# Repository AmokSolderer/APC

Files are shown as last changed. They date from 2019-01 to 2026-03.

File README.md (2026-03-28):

# The Arduino Pinball Controller

Before I explain what the APC is, let's first clarify what it is not.
 
The APC is no commercial drop-in replacement board. It is intended for people with some basic knowledge of programming and electronics who want to expand the possibilities of their pinball machine.

As this is a private project with no commercial interest, you may use the APC at your own risk and I'm not liable for any damage that might occur to your machine while using it.  
Some special machines might even not work with the APC or require additional HW. Please check the [Known issues](https://github.com/AmokSolderer/APC#known-issues) section for details.

## Overview

The APC is a freely programmable controller for Williams pinball machines. It uses an Arduino Due and contains all the circuitry required to run a Williams pinball machine from System 3 to System 11c (and the compatible Data East machines):

* Display interface for all corresponding display types
* 24 Solenoid drivers
* Lamp matrix drivers for 64 lamps
* Switch matrix drivers for 64 switches + 8 non matrix switches
* SD card interface (to store audio files, highscores and settings)
* Audio amplifier with two channels (to play music and sound effects simultaneously / can be changed to single channel stereo)

To summarize the above it can be said that the APC does replace all CPU, power driver and sound related boards at a price of well below 100€ per board. 

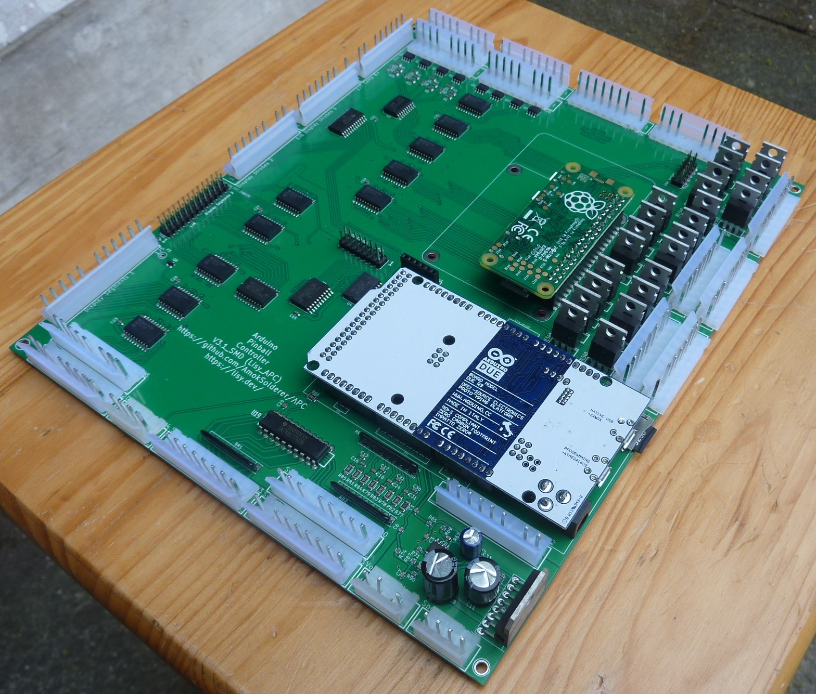
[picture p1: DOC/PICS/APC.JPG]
APC 2.0


The picture shows an APC 3.1 board with the new on-board SD-Card slot below the Arduino.  
See my [APC 3 video](https://www.youtube.com/watch?v=4EgOTJyxMXo) to get an impression what this board can do.

There's a table of contents of the available documentation at the end of this page.

### Special features

* Hardware extensions interface. The pinout is compatible to the Sound Overlay Solenoid Board used in games like Whirlwind, but it is upgraded a bit to support all kind of self made hardware
* A socket for a Raspberry Pi which can be used to run PinMame on the APC board. With this you can run the original ROM code on your APC.
* [PinMameExceptions](https://github.com/AmokSolderer/APC/blob/master/DOC/PinMameExceptions.md) are game specific code blocks that act like a man-in-the-middle between the game HW and PinMame. That means even if your game is running in PinMame you can still introduce some changes. Take a look at my [Jungle Lord video](https://www.youtube.com/watch?v=bbfhH_-gMfE) or my [Comet ball saver](https://youtu.be/JbgMa_pn0Lo) to see how a few lines of code can change a game dramatically.

Typical examples for the use of PinMameExceptions are:

* Pre System11 games usually use just one audio channel which can even be annoying at times. With PinMameExceptions you can add [a background music track](https://github.com/AmokSolderer/APC/blob/master/DOC/PinMameSound_3_7.md#adding-background-music) which replaces the original background sound. The change is easy and for most pre System11 which have PinMameExceptions it's already implemented. Check [this list](https://github.com/AmokSolderer/APC/blob/master/DOC/PinMame.md#available-sounds) for details.
* Add a ball saver. There's a [general ball saver](https://github.com/AmokSolderer/APC/blob/master/DOC/PinMameExceptions.md#how-to-add-a-ball-saver) available which can be easily adapted to your machine. Of course you can also add an individual ball saver - all you have to do is not to tell PinMame that the ball has reached the outhole, but to kick it into the plunger lane instead. Watch my [Comet video](https://youtu.be/JbgMa_pn0Lo) to see how it can be done with just a few lines of code.  
Check the [description](https://github.com/AmokSolderer/APC/blob/master/DOC/PinMameExceptions.md#how-to-add-a-ball-saver) to see how both options work.
* Add HW toys like a shaker motor or flashers and the necessary rules to drive them. If your game has no free solenoid drivers left, then just add the [Solenoid expansion board](https://github.com/AmokSolderer/APC/blob/master/DOC/SolExpBoard.md) to get 8 more. You can also use the [LED expansion board](https://github.com/AmokSolderer/APC/blob/master/DOC/LEDexpBoard.md) to control RGB-LED stripes or just connect your own individual HW.

The picture below shows an APC prototype in my Pinbot.

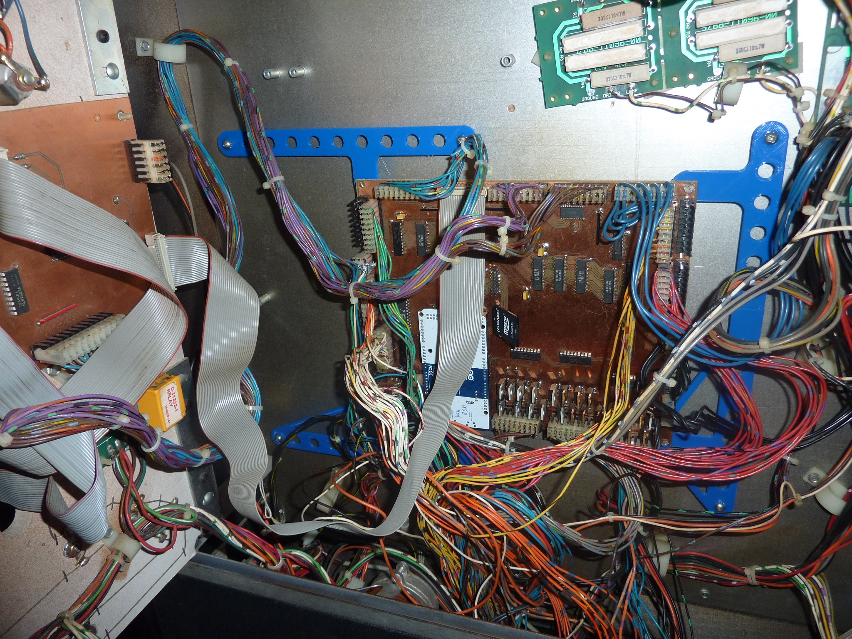
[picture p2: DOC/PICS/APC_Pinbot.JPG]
Pic Pinbot


To see the APC in an early stage you might want take a look at my [Black Knight game video](https://youtu.be/N5ipyHBKzgs)

## Game Software

### PinMame

You can use [Lisy](https://lisy.dev/apc.html) to run PinMame on an APC board. This spares you the effort to do any game Software as you can run the old ROM code.
For System 3 - 7 machines the APC can be used with the old original soundboards. That means in this case it's a plug & play solution.
You might want the APC to generate the audio anyway, either because you don't have an audio board, you want to do your own sounds or you have a System 9 or 11 game. In this case it's going to require some work to set up your game with PinMame. Take a look at the [PinMame Sound page](https://github.com/AmokSolderer/APC/blob/master/DOC/PinMame.md) to see what I mean.

With PinMame running for your game you can use the [PinMameExceptions](https://github.com/AmokSolderer/APC/blob/master/DOC/PinMameExceptions.md) functionality of the APC to change the rules of your game even though it's running under PinMame control.  
Watch my [Jungle Lord video](https://www.youtube.com/watch?v=bbfhH_-gMfE) so see an example. The corresponding code can be found in PinMameExceptions.ino in the AmokPrivate branch on Github.  
Another example is the ball saver I [added to my Comet](https://youtu.be/JbgMa_pn0Lo).

### MPF

For those who want to do their own game rules without having to use C, the APC does support the [Mission Pinball Framework](http://missionpinball.org/). It can run on a PC which then controls the APC via USB.

I did a short video with some basic [MPF setup](https://github.com/AmokSolderer/APC/tree/master/DOC/Software/MPF) to test that everything is working:

[MPF runs APC](https://www.youtube.com/watch?v=w4Po8OE5Zkw)

### C code

If you're familiar with C you can also program the APC directly. This SW would then run on the Arduino itself with no need for an additional PC or Raspberry Pi.  
For this the APC software offers an [API](https://github.com/AmokSolderer/APC/blob/master/DOC/Software/APC_SW_reference.pdf) providing the necessary commands to control a pinball machine. It's still a lot of effort to program a game completely from scratch, but you could even run your game in PinMame and only use the API to do changes or extensions to the original rules.

You don't necessarily have to do the code from scratch. There is a [Base Code](https://github.com/AmokSolderer/APC/blob/master/BaseCode.ino) which covers the basics of a pinball machine and can be used as a starting point.  
Furthermore there're the above mentioned [PinMameExceptions](https://github.com/AmokSolderer/APC/blob/master/DOC/PinMameExceptions.md) which can change a game dramatically with just a few lines of code.

## Hardware

The APC hardware status is mature. I have version 2.0 in use since January 2018 without anything to complain about. Since then the HW has basically stayed the same, just some features have been added and the board has been prepared for automatic assembly.
You can find the schematics, BOM and layout data in the [hardware section](https://github.com/AmokSolderer/APC/tree/master/DOC/Hardware). There have been some minor HW updates which are explained in the [Changelog](https://github.com/AmokSolderer/APC/blob/master/DOC/Changes.md).

The APC features an HW extensions interface which is an 8 bit bus with several enable signals. At the moment there're two extension board available, but you could use it for all kinds of additional hardware.

The first board is an LED expansion board to control WS2812 based LED-Strips with the APC. For more information about this board please refer to the [APC LED expansion board](https://github.com/AmokSolderer/APC/blob/master/DOC/LEDexpBoard.md) section.

The following picture shows the APC in a Comet with the LED Expansion board connected to the hardware extensions interface.

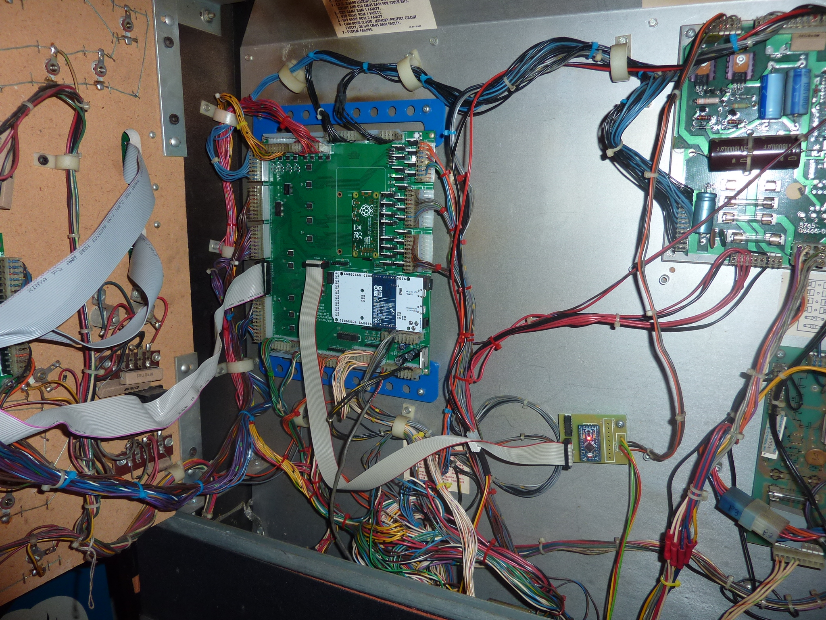
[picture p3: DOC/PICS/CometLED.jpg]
APC Comet LED


A short video with this setup can be found here : 

[GI LEDs](https://youtu.be/kLWVUdhSwfo)

The second board is a [driver for 8 additional solenoids](https://github.com/AmokSolderer/APC/blob/master/DOC/SolExpBoard.md). The current version is mainly suited for use with an own power supply (e.g. for 24V shaker motors).

I use [special alphanumerical displays](https://github.com/AmokSolderer/APC/blob/master/DOC/Sys7Alpha.md) in my Black Knight which can also be found in the HW section as well as an LED replacement for the original System7 numerical displays.

## Supported machines

The following table gives an overview about the various system generations the APC can be used with and if at least one machine of each generation has been confirmed to work with it. Additionally you can see whether PinMame or [MPF](http://missionpinball.org/) have been tested with at least one machine of this generation and whether some special preparation like additional cables are required. Details about these cables can be found [here](https://github.com/AmokSolderer/APC/blob/master/DOC/HowToStart.md#cable-extensions)

The PinMame support is still under development and even if a generation is basically supported you still need the audio files for your particular game. A list of available audio files and a description how to extract your own files can be found on the [PinMame page](https://github.com/AmokSolderer/APC/blob/master/DOC/PinMame.md).

| Williams System | Tested  | PinMame support | MPF support | Comment |
|--|--|--|--|--|
|3| Yes | Yes | Yes|When PinMame is used, some solenoid activation times need to be increase by a [PinMameException](https://github.com/AmokSolderer/APC/blob/master/DOC/PinMameExceptions.md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)|
|4| Yes | Yes | Yes|When PinMame is used, some solenoid activation times need to be increase by a [PinMameException](https://github.com/AmokSolderer/APC/blob/master/DOC/PinMameExceptions.md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)|
|6| Yes | Yes | Yes |When PinMame is used, some solenoid activation times need to be increase by a [PinMameException](https://github.com/AmokSolderer/APC/blob/master/DOC/PinMameExceptions.md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)|
|7| Yes | Yes | Yes | Needs two additional wires |
|9| Yes | Yes | Yes |  |
|11| Yes | Yes | Yes |  |
|11a| Yes | Yes | Yes | Some cable ties have to be cut and the wiring harness opened a bit |
|11b| Yes | Yes | Yes | Some cable ties have to be cut and the wiring harness opened a bit |
|11c| Yes | Yes | Yes | The wires of three connectors must be extended |

The following Data East MPUs are almost identical to their counterparts from Williams but DE used 2.1 audio boards. Check the [known issues](https://github.com/AmokSolderer/APC#known-issues) for details

| Data East Version | Tested  | PinMame support | MPF support | Comment |
|--|--|--|--|--|
|1| Not yet | Yes | Yes | audio needs a cable adapter and is only mono |
|2| Not yet | Yes | Yes | audio needs a cable adapter and is only mono |
|3| Yes | Yes | Yes | Only non DMD machines / audio needs a cable adapter and is only mono / probably some [cable extensions](https://pinside.com/pinball/forum/topic/arduino-pinball-controller/page/18#post-6846714) are needed |

## Changes / What's new?

A history of the recent changes can be found in the [Changelog](https://github.com/AmokSolderer/APC/blob/master/DOC/Changes.md)

## Known issues

### Stereo audio

Some games like Jokerz! or Data East games starting from MPU version 1 have stereo or even 2.1 audio boards. These are currently not supported by the APC SW.  
From the HW point of view, the APC is capable of generating two independent sound channels which could also be used for stereo. But up to now they're used to generate separate channels for sounds and music which are combined in the output amplifier.  
In order to use these machines with the APC you'd have to build a cable adapter and the audio would only be mono.

### Stepper motors

Games like Jokerz! or Riverboat Gambler use stepper motors to drive a wheel in the backbox and the amount of steps being generated determine where the wheel stops.  
Alas, there's a problem with Lisy/PinMame not sending all steps to the APC. This means it is not possible for the APC to determine at which position the wheel is supposed to stop.  
Note that this is not a problem of the APC itself, but occurs only when Lisy/PinMame is used. If you program your game code in C there won't be any problems.

### Rollergames music problems

The Rollergames implementation in PinMame has a bug in the music control. For some reason a new music track is started every few seconds. Most of the time it's the same track that's already running. I have therefore implemented a workaround in the PinMameExceptions of the Rollergames which prevents that the running music track can be restarted. This improves the situation somehow, but more sophisticated PinMameExceptions are needed to really fix this.  
Up to now only Rollergames seems to be affected, other machines using the same audio boards are working fine.

## Feedback

Feedback is very important for me, also to learn where additional documentation is needed. There're still features that are undocumented because I just don't have the time (and motivation) to write the docs.  
Hence, I've limited my documentation effort to a minimum, but I'm willing to provide additional docs and hints on request. Please use the forum links below for these requests.  

**So if you're interested please leave some feedback in the [Flippertreff forum (german)](https://www.flippertreff.de/start/forum/topic/11356-arduino-pinball-controller/) or in the  - [Pinside Form (english)](https://pinside.com/pinball/forum/topic/arduino-pinball-controller#post-4898318).**

## How to get startet?

I'm sorry, but I'm not going to sell any boards. Check whether anyone in the above mentioned forums has a spare board for sale. If this fails you can still order populated boards from China.  
If you're interested in using an APC, then be sure to follow the instructions given in the first part of the documentation listet below. They will guide you through the process of getting and setting up an APC board.

## Documentation contents

1. Building and setting up an APC  
1.1. [The APC board](https://github.com/AmokSolderer/APC/blob/master/DOC/APC_board.md) - How to get one and how to set it up  
1.2. [Upload the SW](https://github.com/AmokSolderer/APC/blob/master/DOC/Upload_SW.md) - How to program the Arduino DUE  
1.3. [Basic Preparation](https://github.com/AmokSolderer/APC/blob/master/DOC/Prepare.md) - Required cables and stuff  
1.4. [Do the tests](https://github.com/AmokSolderer/APC/blob/master/DOC/InitialTests.md) - Test your board  
1.5. [Run a game](https://github.com/AmokSolderer/APC/blob/master/DOC/RunGame.md) - All the ways to get a game running  

2. References  
2.1. [Setting up the BaseCode](https://github.com/AmokSolderer/APC/blob/master/DOC/SetUpBC.md) - Do the BaseCode setup to get a very simple game  
2.2. [Useful software tools](https://github.com/AmokSolderer/APC/blob/master/DOC/UsefulSWtools.md) - Simple tools for audio data conversion and so on  
2.3. [APC settings](https://github.com/AmokSolderer/APC/blob/master/DOC/Settings.md) - a table of the settings and how to use them  
2.4. [APC schematics](https://github.com/AmokSolderer/APC/blob/master/DOC/Hardware/APC_schematics.pdf) - just in case you want to know what you're about to build  
2.5. [If things don't work](https://github.com/AmokSolderer/APC/blob/master/DOC/Problems.md) - If you have a problem, check here first  
2.6. [APC specialties](https://github.com/AmokSolderer/APC/blob/master/DOC/Specialties.md) - How special switches and the flipper relay are handled by the APC

3. Writing my own game code - You want to program your own game in C? Then read this.  
3.1. [Game code tutorial](https://github.com/AmokSolderer/APC/blob/master/DOC/GameCodeTutorial.md) - A step by step introduction to writing your own game code  
3.2. [APC software reference](https://github.com/AmokSolderer/APC/blob/master/DOC/Software/APC_SW_reference.pdf) - All commands of the API in a nutshell  

4. Running PinMame  
4.1. [Lisy Homepage](https://lisy.dev/apc.html) - Location of the Lisy SW download and more  
4.2. [PinMame Sound](https://github.com/AmokSolderer/APC/blob/master/DOC/PinMame.md) - shows whether your game is supported and what to do if not  
4.3. [PinMame System 3 - 7 Sound howto](https://github.com/AmokSolderer/APC/blob/master/DOC/PinMameSound_3_7.md) - How to enable the sound of System 3 - 7 games  
4.4. [PinMame System 9 Sound howto](https://github.com/AmokSolderer/APC/blob/master/DOC/PinMameSound_9.md) - How to enable the sound of System 9 games  
4.5. [PinMame System 11 Sound howto](https://github.com/AmokSolderer/APC/blob/master/DOC/PinMameSound_11.md) - How to enable the sound of System 11 games  
4.6. [PinMameExceptions](https://github.com/AmokSolderer/APC/blob/master/DOC/PinMameExceptions.md) - change your game, but let PinMame do the main work  
4.7. [PinMame game numbers](https://github.com/AmokSolderer/APC/blob/master/DOC/lisyminigames.csv) - list of the PinMame game numbers  
4.8. [Controlling Lisy](https://github.com/AmokSolderer/APC/blob/master/DOC/LisyDebug.md) - updating Lisy and using the debug mode  
4.9. [Automatic sound file generation](https://github.com/AmokSolderer/APC/blob/master/DOC/SoundAuto.md)  
5.0. [Manual sound file generation](https://github.com/AmokSolderer/APC/blob/master/DOC/SoundManual.md)  
5.1. Another way [for extracting sound files](https://github.com/AmokSolderer/APC/blob/master/DOC/PinMameSounds.md) - automatic extraction of sound files and the use of Audacity in more detail (by Mokopin)

5. Using MPF  
5.1. [MPF runs APC](https://www.youtube.com/watch?v=w4Po8OE5Zkw) - see my first humble MPF steps in this video  
5.2. [MPF setup](https://github.com/AmokSolderer/APC/tree/master/DOC/Software/MPF) - my MPF test config files

6. Additional APC hardware - boards and other stuff that might come in handy with the APC  
6.1. [APC LED expansion board](https://github.com/AmokSolderer/APC/blob/master/DOC/LEDexpBoard.md) - a board to control WS2812 based LED strips with the APC  
6.2. [APC solenoid expansion board](https://github.com/AmokSolderer/APC/blob/master/DOC/SolExpBoard.md) - to control additional features  
6.3. [System 7 alphanumeric display](https://github.com/AmokSolderer/APC/blob/master/DOC/Sys7Alpha.md) - to have alphanumerical displays in a pre System 11 machine  
6.4. [Installation frames](https://github.com/AmokSolderer/APC/blob/master/DOC/Frames.md) - to mount the APC in your backbox  

7. Additional non APC hardware - just some stuff I designed over the years. Can also be used without the APC  
7.1. [System 7 LED display](https://github.com/AmokSolderer/APC/blob/master/DOC/DispSys7.md) - an LED replacement display for System 7, purely numerical  
7.2. [System 11 LED display](https://github.com/AmokSolderer/APC/blob/master/DOC/DispSys11.md) - an LED replacement display for System 11  
7.3. [System 11a LED display](https://github.com/AmokSolderer/APC/blob/master/DOC/DispSys11a.md) - an LED replacement display for System 11a and early 11b  
7.4. [System 11b LED display](https://github.com/AmokSolderer/APC/blob/master/DOC/DispSys11b.md) - an LED replacement display for later System 11b and 11c  

8. APC games - Complete games running natively on the APC or games that run in PinMame but have been changed  
8.1. [Black Knight](https://github.com/AmokSolderer/APC/blob/master/DOC/BlackKnight.md) - Complete game code with some additional features  
8.2. [Pinbot](https://github.com/AmokSolderer/APC/blob/master/DOC/Pinbot.md) - Complete game code with some additional features  
8.3. [Comet](https://github.com/AmokSolderer/APC/blob/master/DOC/Comet.md) - Some extensions to the original game code running in PinMame

9. Videos - For the generation Youtube  
9.1. [What's new in APC3](https://youtu.be/4EgOTJyxMXo) - Gives an overview about what the APC is and what version 3 can do  
9.2. [Lisy, APC and PinMame](https://youtu.be/cXrh-XPqCKw) - Shows the use of PinMame in an early stage  
9.3. [PinMameExceptions](https://youtu.be/bbfhH_-gMfE) - What is a PinMameException and how does it work?  
9.4. [Adding a ball saver with PinMameExceptions](https://youtu.be/JbgMa_pn0Lo) - Another example of how to use PinMameExceptions  
9.5. [APC MPF](https://youtu.be/w4Po8OE5Zkw) - A simple demonstration of the APC being controlled by MPF  
9.6. [GI LEDs](https://youtu.be/kLWVUdhSwfo) - Shows the LED_exp board in action  
9.7. [Arduino Pinball Controller hardware extensions interface](https://youtu.be/8BnVTpKq-2Y) - Also shows the use of the LED_exp board, but in an early SW stage  
9.8. [APC Black Knight demo](https://youtu.be/N5ipyHBKzgs) - My first APC video. Not really up to date any more, but it shows the basics  
9.9. [How to use numerical displays](https://youtu.be/2A5Tt9FQ2as) - How to navigate the menus when you can't read any text  
9.10. [How to adjust the display setting to a 2x16 alphanumerical display](https://youtu.be/XqPWbm-HWM8) - How to find the right setting to make these displays work

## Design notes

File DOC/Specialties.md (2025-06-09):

# APC specialties

Usually the APC handles the pinball hardware quite straightforward. That means the lamp, switch and solenoid numbers used by the APC are the same as printed in the manual of your pinball machine, no matter whether you use MPF, Lisy/PinMame or write your own C code.  
However, there're some specialties which are handled in this section.

## Special switches

Williams assigned numbers only to Switches which belong to the switch matrix.  
The APC assigns numbers > 64 to the rest of them, so they can be used as normal switches:

| APC switch number | Williams equivalent |
|--|--|
| 65 | Activation switch for special solenoid 1 |
| 66 | Activation switch for special solenoid 2 |
| 67 | Activation switch for special solenoid 3 |
| 68 | Activation switch for special solenoid 4 |
| 69 | Activation switch for special solenoid 5 |
| 70 | Activation switch for special solenoid 6 |
| 71 | Memory Protect switch |
| 72 | Advance switch |
| 73 | Up/Down switch (active when the switch is in Up position) |

Additional information about these switches is provided below:

### Special solenoids and their switch numbers

Williams machines from System3 to System 11a have so called special solenoids. Each of these solenoids is connected to a special switch which will fire the solenoid immediately without any involvement of the CPU. This means that those special switches are not part of the switch matrix (which is CPU controlled). They are handled by a dedicated logic, are not visible for the CPU and therefore have no numbers.  
If your switch matrix has a switch for a special solenoid anyway, then it's because the CPU needs to know when it is triggered (e.g. for scoring). It's a second switch additional to the special solenoid switch. For example: in case of a pop bumper, the plastic disc to trigger the bumper is usually connected to the special solenoid switch and the scoring switch is triggered by the bumper ring being pulled down by the solenoid.  
This means that you have to select the special solenoid switch as the activation switch for your pop bumper, because the scoring switch is only activated when the solenoid is already moving.

The APC handles special solenoid switches as normal switches, but their numbers start with 65 which is the trigger switch for special solenoid 1.  

Williams dropped the special solenoid switches with the start of System 11b. After that the activation switches were part of the switch matrix and controlled by the CPU.

### The Advance, Memory Protect and Up/Down switch

Similar to the special solenoid switches, the Advance, Memory Protect and Up/Down switch are also not part of the switch matrix. The APC assignes the numbers > 70 to them. Note that the Up/Down switch is low active, which means that it's active when NOT pressed.

## The flipper relay

In the original Williams HW the flipper relay switches both flipper fingers at once and has no solenoid number.  
The APC doesn't use a relay but switching transistors. There's one for the left and one for the right flippers, so it is possible to activate the sides individually.  
Their solenoid numbers are 23 and 24, but any (de-)activation command sent to solenoid 25 will affect both flipper fingers.

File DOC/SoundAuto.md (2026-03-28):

# Automatic sound file generation

## Automatic extraction from PinMame

In PinMame, press F4 to enter the 'Sound Command Mode' then press DEL for the Manual / Command Mode.

Now enter the audio command you want PinMame to start with, for audio board 0 this would be 000000000000 and 000000000100 for audio board 1. Press F6 to start the automatic extraction. PinMame will go through the audio command one by one and generate .wav files of them.  
This should generate most of the sound files, but there're limits especially for System11. The music files for example are sometimes truncated, so you'd have to extract them manually. This is not a big deal because there're just a few of them, usually starting with the audio command 000000000101.  
Another problem with early System11 is that PinMame cannot find all sounds for audio board 1. You could try to guide it by using additional start commands like 000000000160, but it's easier to just leave it for now and if you get an error message like '1_85.snd not found' during your first games then you know that starting another extraction with 000000000180 should do the trick.

## Automatic renaming

Files generated with this method get names which include the audio command number and the machine name (e.g. 0x00A5-fire_l3.wav). However, the APC needs the names in the format [single digit board prefix]_[sound number in hex].wav, so the correct name for this sound would be 0_a5.wav. With Linux you can just use the rename command which should be part of most distributions and is very powerful. Windows users would have to install some bulk renaming tool.  
On our case we need to use

    rename -v -n 's/0x00//' *         to remove the '0x00' at the start of the filename
    rename -v -n 's/-fire_l3//' *     to get rid of the rom name
    rename -v -n 'y/A-Z/a-z/' *       to replace upper case by lower case letters
    rename -v -n 's/^/0_/' *          to add the board prefix '0_'

The actions will be done for all files in the current directory. Note that the -v -n options will issue a dry run, so the tool will just show you the new names without actually doing anything.

## Automatic processing with Audacity

Basically you have to do the same steps as described in the [manual way of sound file preparation](https://github.com/AmokSolderer/APC/blob/master/DOC/SoundManual.md), but you'd use a macro to process all files in your working directory. An example macro for processing callouts would look like this:

    Select:End="0,15" Mode="Set" RelativeTo="ProjectStart" Start="0"
    Delete:
    Select:End="0" Mode="Set" RelativeTo="ProjectEnd" Start="0,05"
    Delete:
    SelectAll:
    Normalize:ApplyGain="1" PeakLevel="0" RemoveDcOffset="1" StereoIndependent="0"
    Amplify:Ratio="1,9952623"
    ExportWav:
    
This will delete 150ms at the beginning, as the automatic extraction sometimes adds a few ms of noise to the start of a sound and 50ms at the end. Then it normalizes the sound to a peak level of 0dB and amplifies even 6dB more. The latter will cause the signal to be distorted, but it's still OK as it will just affect the peaks and callouts need to be quite loud to be still audible when the BG music plays.

These are just example values I used for one specific machine. You generally have to find out for yourself what the best relation in terms of volume is for the BG music, the callouts and the general sound effects.

## Sampling Rate

Windows users will additionally have to set the sampling rate to the standard 44.1KHz, as the Windows PinMame uses 48KHz by default. This cannot be batched processed in Audacity, so you'd have to use a tool like [OCENAUDIO](https://www.ocenaudio.com) for this.

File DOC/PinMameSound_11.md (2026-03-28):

# System 11

The first System11 machines had two independent audio circuits, each containing a processor and sound EPROMS. One of these circuits was located on the main CPU board while the other was on a seperate audio board. PinMame distinguishes these boards by using two audio prefixes which can be selected by 00 and 01 in PinMame's 'Sound Command Mode'. Both of these prefixes offer different sound commands.
The table below shows the special commands of the Pinbot audio system that we know about. There might still be some gaps, but it's enough to make the Pinbot work.  
So if you have additional information to fill these gaps please tell us and we're going to include it.

For this documentation I expect the other System 11 machines to work in a similar way.

|Prefix|Command / Hex|Comment|
|--|--|--|
|00|00|Stop Sound|
|01|00|Stop Music|
|01|01 - 08|Looped music tracks, some of them have an intro before the looping part begins|
|01|40 - 42|Transistions and endings for looped music|
|01|7f|Stop sounds of prefix 01|
|01|6X|Music volume setting 0x60 is full volume 0x64 is almost nothing|

## Sound files

There're multiple ways to obtain the original sounds for System 11 machines. Some can be found on the internet, directly recorded from your pinball machine or you can extract them from PinMame. What ever you do, the result should be a mono WAV file with 44.1KHz sampling rate and reasonable amplitude.  
If you find the files on the internet you can proceed to the [Audio file conversion](https://github.com/AmokSolderer/APC/blob/master/DOC/PinMameSound_11.md#audio-file-conversion) section, as you don't have to extract them from PinMame.

## Automatic sound file preparation

There're several methods to automatically extract WAV files from PinMame and batch process them to work with the APC. Using this, it just takes me 2 - 3 hours to generate the files for an early System11 machine  
My way of doing this is described [here](https://github.com/AmokSolderer/APC/blob/master/DOC/SoundAuto.md). Since I'm using Linux, things might be a bit different for Windows users, as they additionally have to adjust the sample rate for example.  
Mokopin (from the Flippertreff forum) has also written some [Instructions for extracting sound files](https://github.com/AmokSolderer/APC/blob/master/DOC/PinMameSounds.md) which explain the automatic extraction of sound files and the use of Audacity for Windows users.

## Manual sound file preparation

This decribes the [manual way of sound file preparation](https://github.com/AmokSolderer/APC/blob/master/DOC/SoundManual.md). I'd recommend to try the automatic way first, because it's much faster. However, the manual way explains what needs to be done and it can be used as a fallback solution, if the automatic way fails. This is usually happens for the music themes of System11 machines. The automatic extraction often truncates those, so these would have to be extracted manually. System11 music themes usually consist of an intro and a looping part, s I'd recommend to manually extract a long music file and use Audacity to split it up accordingly. The correct naming for such music themes will be handled the PinMameExceptions section below.

## Volume levels

Callouts are sensitive and need to be quite loud in order not to get lost in the music. Hence, it makes sense to load a music theme and a callout into Audacity and play them simultaneously. I usually amplify the callouts to +6dB (accepting the minor distortion caused by this) and choose the volume of the music themes as high as possible for the callout to still sound well. The other sounds can usually have the same volume level as the BG music.

## Audio file conversion

Put all preprocessed WAV files in one folder, check that the names are correct and execute the [AudioSaveFolder.pl](https://github.com/AmokSolderer/APC/blob/master/DOC/UsefulSWtools.md) tool.  
The resulting .snd files must be copied to the APC's SD card. Please format your card before with a special SD card formatting tool from the SD Association (sdcard.org) to improve the card's access times.

If you start your game now you should already hear most of the sounds, but everything out of the ordinary like correct music handling and so on won't work correctly. We need to tell the APC about these special sound sommands and how to deal with them. 

## PinMameExceptions for audio

The APC features a machine specific exception handling, which means that you can manipulate your game even though it is running in PinMame. The exceptions are written in C and are using the commands of the APC SW framework. More information about the framework can be found in [the tutorial](https://github.com/AmokSolderer/APC/blob/master/DOC/GameCodeTutorial.md) and the [APC software reference](https://github.com/AmokSolderer/APC/blob/master/DOC/Software/APC_SW_reference.pdf).

To enable PinMameExceptions for your machine you have to add a game specific section to the PinMameExceptions.ino file and recompile the SW.
You can manipulate sound, lamp, switch, display and solenoid commands. Some of these expections are necessary to make your machine work correctly, but you can also do improvements or moderate rule changes.

In the case at hand we're using these exceptions to tell the APC what to do when a certain audio command is issued by PinMame. I'm using the Pinbot as an example here.

### Setting up PinMameExceptions for the Pinbot

The following steps have been done by me to make my Pinbot work correctly. That means you can find the code which is described here in PinMameExceptions.ino.

There's a template named

    byte EX_Blank(byte Type, byte Command)

in PinMameExceptions.ino to be used as a starting point. So let's create a copy of this and rename it to

    byte EX_Pinbot(byte Type, byte Command)

In order for the system to use this code section, we have to add it to EX_Init which is at the end of PinMameExceptions.ino and determines which code is used for which machine. The games are being distinguished by their [PinMame game number](https://github.com/AmokSolderer/APC/blob/master/DOC/lisyminigames.csv). Hence we have to add a case 43 for the Pinbot.

    void EX_Init(byte GameNumber) {
      switch(GameNumber) {
      case 20:                                            // Jungle Lord
        EX_EjectSolenoid = 2;                             // specify eject coil for improved ball release
        PinMameException = EX_JungleLord;                 // use exception rules for Jungle Lord
        break;
        break;
      case 39:                                            // Comet
        PinMameException = EX_Comet;                      // use exception rules for Comet
        break;
      case 43:                                            // Pinbot
        PinMameException = EX_Pinbot;                     // use exception rules for Pinbot
        break;
      case 44:                                            // F-14 Tomcat
        PinMameException = EX_F14Tomcat;                  // use exception rules for Tomcat
        break;
      default:
        PinMameException = EX_DummyProcess;}}

All games not listet here do not have exceptions defined yet, so the exception pointer just points to a dummy process which only plays the standard sounds, but knows no exceptions.

### Handling ordinary sounds
    
As Pinbot uses two audio boards, we need to define a SoundCommandCh1 and a SoundCommandCh2 case in our EX_Pinbot program. Hence you can delete all cases except of these two and the default case. The result should look like this:

    byte EX_Pinbot(byte Type, byte Command){               // use this as a template and an example of how to add your own exceptions
      switch(Type){                                       // usually just a few exception cases are needed, just delete the rest
      case SoundCommandCh1:                               // sound commands for channel 1
        if (Command == 38){                               // sound command 0x26
          // enter your special sound command 0x26 here
        }
        else {
          char FileName[9] = "0_00.snd";                  // handle standard sound
          if (USB_GenerateFilename(1, Command, FileName)) { // create filename and check whether file is present
            PlaySound(51, (char*) FileName);}}
        return(0);                                        // return number not relevant for sounds
      case SoundCommandCh2:                               // sound commands for channel 2
        if (Command == 38){                               // sound command 0x26
          // enter your special sound command 0x26 here
        }
        else {
          char FileName[9] = "1_00.snd";                  // handle standard music
          if (USB_GenerateFilename(2, Command, FileName)) { // create filename and check whether file is present
            PlayMusic(51, (char*) FileName);}}
        return(0);                                        // return number not relevant for sounds
      default:                                            // use default treatment for undefined types
        return(0);}}
    
For System11c games with only one audio board you can remove the SoundCommandCh1 case also.  
What we have now is a default handler for all the sound numbers that have no exceptions defined. The filenames of these sounds just consist of the channel number (prefix), an underscore and the sound number in hex followed by ".snd". There is a routine called

    byte USB_GenerateFilename(byte Channel, byte Sound, char* FileName)

which adds the hex code to a given filename and handles the display messages if the audio debug mode is active. It returns a 1 in case the soundfile does exist and a 0 if it doesn't. Is is therefore only necessary to play the sound when the return value has been 1.

In EX_Blank the 'if' for sound command 38 is just meant as an example to make it clear where exceptions have to be added, but for the Pinbot we can change this to incorporate the Sound Stop command (00) for each channel:

    byte EX_Pinbot(byte Type, byte Command){               // use this as a template and an example of how to add your own exceptions
      switch(Type){                                       // usually just a few exception cases are needed, just delete the rest
        if (!Command){                                    // sound command 0x00 - stop sound
          AfterSound = 0;
          StopPlayingSound();}
        else {
          char FileName[9] = "0_00.snd";                  // handle standard sound
          if (USB_GenerateFilename(1, Command, FileName)) { // create filename and check whether file is present
            PlaySound(51, (char*) FileName);}}
        return(0);                                        // return number not relevant for sounds
      case SoundCommandCh2:                               // sound commands for channel 2
        if (!Command) {                                   // sound command 0x00 - stop music
          AfterMusic = 0;
          StopPlayingMusic();}
        else {
          char FileName[9] = "1_00.snd";                  // handle standard music
          if (USB_GenerateFilename(2, Command, FileName)) { // create filename and check whether file is present
            PlayMusic(51, (char*) FileName);}}
        return(0);                                        // return number not relevant for sounds
      default:                                            // use default treatment for undefined types
        return(0);}}

Note, that the APC refers to it's two channels as the Sound and Music channel and the commands are named accordingly. Check the [APC software reference](https://github.com/AmokSolderer/APC/blob/master/DOC/Software/APC_SW_reference.pdf) for more information.

### Handling music

Most of the music scores of System11 machines consist of an intro and a looping part which is repeated all over. If you want it easy, you could just put the intro and some repetitions of the looping part in one file. This will work in most cases, but if you wait long enough the music will just run out.
In order to prevent this from happening, the intro and the looping part must be in separate files and an exception rule must handle the sequencing.

Let's use music track 4 from Pinbot as an example. In the SoundCommandCh2 case the following code handles track4:

    else if (Command == 4) {                          // music track 4
      PlayMusic(50, "1_04.snd");                      // play non looping part of music track
      QueueNextMusic("1_04L.snd");}                   // queue looping part as next music to be played

When audio channel 2 receives command 4 then the intro 1_04.snd is played first and the QueueNextMusic command is used to queue the looping part 1_04L.snd to be played after the intro has run out. As long as the AfterMusic variable is not set to zero, the looping part will be repeated automatically.

Such a rule needs to be present for each music score your machine features.

Note that if you're machine is using vocals as part of the music then these have to be mixed into the music. The reason for this is explained [here](https://github.com/AmokSolderer/APC/blob/master/DOC/PinMameSound_11.md#special-cases).

### Implementing music volume

System11 machines are reducing the volume of their music track when certain sounds are played. This is done by sending the 0x6X command with the prefix of the music board. 0x60 is the code for full volume and 0x61 and so on for less volume. The granularity might differ for the various System11 generations, so you might want to adapt this for your game. However, for Pinbot 0x64 is already almost inaudible.  
The APC handles the volume of the music by the MusicVolume variable. A value of zero means full volume and every count up cuts the amplitude by half. Hence, the corresponding code looks like this:

    else if (Command > 95 && Command < 100) {         // music volume command 0x6X
      MusicVolume = Command - 96;}

### Dealing with priorities

Normally a sound is stopped by another sound being requested for the same channel. This is fine for the majority of the sounds, but sounds like speech are more important than others and we don't want the APC to cut them. Hence, we have to define priorities for those sounds which are more (or less) important than others.  
In Pinbot's case all sound numbers higher than 128 requested with prefix 0 are callouts and are therefore called with a priority of 51 instead of the 50 which is used for the rest:

    else {                                            // proceed with standard sound handling
      char FileName[9] = "0_00.snd";                  // handle standard sound
      if (USB_GenerateFilename(1, Command, FileName)) { // create filename and check whether file is present
        if (Command < 128) {                          // play speech with a higher priority
          PlaySound(50, (char*) FileName);}
        else {
          PlaySound(51, (char*) FileName);}}}

Check the [APC software reference](https://github.com/AmokSolderer/APC/blob/master/DOC/Software/APC_SW_reference.pdf) for more information about priorities.

### Dealing with unknown commands

There're still several commands we don't know the meaning of. If you find out what they do please drop us a note, but for the time being we can just ignore them (which worked quite well so far). So for every command that doesn't produce a sound in PinMame, just add a line like 

    else if (Command > 29 && Command < 48) { }        // ignore unknown sound commands 0x1d to 0x30

to prevent them from causing 'File not found' messages on your display.

### The result

The final result is shown below. It contains the PinMameExceptions needed to make the audio for Pinbot work.

    byte EX_Pinbot(byte Type, byte Command){
      switch(Type){
      case SoundCommandCh1:                               // sound commands for channel 1
        if (!Command){                                    // sound command 0x00 - stop sound
          AfterSound = 0;
          StopPlayingSound();}
        else if (Command == 85) { }                       // ignore sound command 0x55
        else if (Command == 105) { }                      // ignore strange misplaced sound during multiball
        else if (Command == 170) { }                      // ignore sound command 0xaa
        else if (Command == 255) { }                      // ignore sound command 0xff
        else {                                            // proceed with standard sound handling
          char FileName[9] = "0_00.snd";                  // handle standard sound
          if (USB_GenerateFilename(1, Command, FileName)) { // create filename and check whether file is present
            if (Command < 128) {                          // play speech with a higher priority
              PlaySound(50, (char*) FileName);}
            else {
              PlaySound(51, (char*) FileName);}}}
        return(0);                                        // return number not relevant for sounds
      case SoundCommandCh2:                               // sound commands for channel 2
        if (!Command) {                                   // sound command 0x00 - stop music
          AfterMusic = 0;
          StopPlayingMusic();}
        else if (Command == 127) {                        // sound command 0x7f - stop sound
          AfterSound = 0;
          StopPlayingSound();}
        else if (Command > 29 && Command < 48) { }        // ignore unknown sound commands 0x1d to 0x30
        else if (Command > 79 && Command < 89) { }        // ignore unknown sound commands 0x4f to 0x59
        else if (Command > 95 && Command < 100) {         // music volume command 0x6X
          MusicVolume = Command - 96;}
        else if (Command == 170) { }                      // ignore unknown sound command 0xaa
        else if (Command == 255) { }                      // ignore unknown sound command 0xff
        else if (Command == 1) {                          // music track 1
          PlayMusic(50, "1_01L.snd");                     // play music track
          QueueNextMusic("1_01L.snd");}                   // track is looping so queue it also
        else if (Command == 2) {                          // music track 2
          PlayMusic(50, "1_02.snd");                      // play non looping part of music track
          QueueNextMusic("1_02L.snd");}                   // queue looping part as next music to be played
        else if (Command == 3) {                          // music track 3
          PlayMusic(50, "1_03L.snd");                     // play music track
          QueueNextMusic("1_03L.snd");}                   // track is looping so queue it also
        else if (Command == 4) {                          // music track 4
          PlayMusic(50, "1_04.snd");                      // play non looping part of music track
          QueueNextMusic("1_04L.snd");}                   // queue looping part as next music to be played
        else if (Command == 5) {                          // music track 5
          PlayMusic(50, "1_05.snd");                      // play non looping part of music track
          QueueNextMusic("1_04L.snd");}                   // queue looping part as next music to be played
        else if (Command == 6) {                          // music track 6
          PlayMusic(50, "1_06.snd");                      // play non looping part of music track
          QueueNextMusic("1_06L.snd");}                   // queue looping part as next music to be played
        else if (Command == 8) {                          // music track 8
          PlayMusic(50, "1_08.snd");                      // play non looping part of music track
          QueueNextMusic("1_01L.snd");}                   // queue looping part as next music to be played
        else if (Command == 10) {                         // music track 0xa
          PlayMusic(50, "1_0a.snd");                      // play non looping part of music track
          QueueNextMusic("1_02L.snd");}                   // queue looping part as next music to be played
        else if (Command == 65) {                         // music track 0x41
          PlayMusic(50, "1_01L.snd");                     // play non looping part of music track
          QueueNextMusic("1_01L.snd");}                   // queue looping part as next music to be played
        else if (Command == 66) {                         // music track 0x42
          PlayMusic(50, "1_0a.snd");                      // play non looping part of music track
          QueueNextMusic("1_02L.snd");}                   // queue looping part as next music to be played
        else if (Command == 148) {                        // music track 0x94
          PlayMusic(50, "1_94.snd");                      // play non looping part of music track
          QueueNextMusic("1_94L.snd");}                   // queue looping part as next music to be played
        else {
          char FileName[9] = "1_00.snd";                  // handle standard sound
          if (USB_GenerateFilename(2, Command, FileName)) { // create filename and check whether file is present
            if (Command < 128) {                          // play only music on the music channel
              AfterMusic = 0;                             // stop looping music
              PlayMusic(50, (char*) FileName);}           // play on the music channel
            else {
              PlaySound(50, (char*) FileName);}}}         // play on the sound channel
        return(0);                                        // return number not relevant for sounds
      default:                                            // use default treatment for undefined types
        return(0);}}                                      // no exception rule found for this type so proceed as normal
    
### Finding out which sounds are still missing

After you have extracted most of the files, there'll be the point when only a few files are still missing and you need to find out their numbers. Of course you could still scan the Lisy log for unknown sound numbers, but in this stage it might be easier to use the 'Audio Debug Mode' of the APC.  
You can activate this mode in the [game settings](https://github.com/AmokSolderer/APC/blob/master/DOC/Settings.md#game-settings-in-remote-control-mode).

In Audio Debug mode the lower display(s) are used for audio information. The Player 3 display (or the left part of the lower display for BK2K type displays) shows information for sound prefix 00 and the Player 4 display (right part of lower display for BK2K) does the same for prefix 01. If the requested sound is found on the SD card, it's hex number is shown in the left side of the corresponding display and the sound is played normally. If the sound file is missing it's hex number is shown on the right side of the corresponding display which makes it easy to find missing sound files.  
As the pre System11 displays cannot show letters, the corresponding sound numbers are shown in decimal values when this kind of display is selected.

By that you can just play your game and only if the number of a missing sound file pops up on the right side of your display you note it down and add it later.

## Sound problems

Most sound problems like lags and stuttering are caused by the performance of the SD card. Take a look at the [If things don't work](https://github.com/AmokSolderer/APC/blob/master/DOC/Problems.md) section for more.

## Special cases 

On the old audio boards each specific kind of sound was generated by special circuitry. For example music was done with synthesizer ICs, speech with special DACs and so on. In total this leads to up to five different, but specialized audio channels which were mixed together eventually.  
Like all modern audio systems, the APC works differently. It has two channels, but doesn't need special audio ICs as every sound can be produced by each channel. In most cases this works quite well, but in some cases we have to adjust the sound files to prevent some sounds from getting lost.

A good example is the music of later System11 games which also include vocals. As the old sound board would produce the music and the voices with different circuits, PinMame will send one command for the music and own commands for each part of the vocals. This will lead to a conflict when additional sounds have to be played simultaneously as the APC has just one channel for sounds. On the other hand, the APC doesn't need a seperation between music and vocals, so we can just use Audacity to mix the vocals into the music file.

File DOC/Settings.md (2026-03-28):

# APC settings

## Selecting the correct display

The preselected display setting is set for the [4 Alpha + Credit display](https://github.com/AmokSolderer/APC/blob/master/DOC/Sys7Alpha.md) which is readable on early System11 displays. However, you'd still need to adjust the display setting and if you have a pre System11 (numbers only) display or a Black Knight 2000 (BK2K / 2 x 16 alphanumeric) you have to get there blindly. To make it easier, the display setting is the very first one.  
To get there you have to keep the Advance key pressed for more than 1s with the Up/Down key being in up position. Wait 4s and then press the Game Start button slowly but repeatedly until you can read the display contents. Pre Sys11 displays cannot show any text, so for the 6 digit displays (Sys3 - 6) a single 7 is shown on the player 4 display. For 7 digit displays (Sys7 and 9) it's an 8.  
After the correct display is selected, press Up/Down to get it down and Game Start to go back one setting to 'Exit Settings'. Now release the Up/Down button and press Game Start again to save the settings and return to the attract mode.

The complete re-initialization of the display is done when you EXIT the system settings. That means your lower row might still look a bit odd even though you've selected the correct display until you exit the settings.

I did two videos to show what I've described above:

[How to use numerical displays](https://www.youtube.com/watch?v=2A5Tt9FQ2as)

[Adjusting the display settings for 2x16 segment System11 displays](https://www.youtube.com/watch?v=XqPWbm-HWM8)

Note that the menus have changed since these videos have been made. So use them only to see how it works in general, but use the tables below as a reference for the settings.

### Using the defaults

Another option is to change the defaults of the settings and remove the corresponding settings file from the SD card.  
To change the display default for example, locate the APC_defaults[64] array in APC.ino which defines the defaults of the 'System Settings':

    const byte APC_defaults[64] =  {0,3,3,1,2,0,0,0,      // system default settings
        64,0,0,0,0,0,0,0,
        0,0,0,0,0,0,0,0,
        0,0,0,0,0,0,0,0,
        0,0,0,0,0,0,0,0,
        0,0,0,0,0,0,0,0,
        0,0,0,0,0,0,0,0,
        0,0,0,0,0,0,0,0};

Every setting is one byte long and they are stored in the same order as listed in the 'System Settings' table below. Hence, if you want to change the 'Display Setting' to a System 3-6 display you would have to change the first byte (number 0) to 7:

    const byte APC_defaults[64] =  {7,3,3,1,2,0,0,0,      // system default settings

The defaults are only used when no settings file is found on the SD card, so you'd have to delete the APC_SET.BIN file if present. 

It works the same way for the Game Settings. The defaults for the game settings in 'Remote Control' mode are located in USBcontrol.ino and the name of the settings file is USB_SET.BIN.

    const byte USB_defaults[64] = {0,0,0,255,0,0,20,0,    // game default settings
                                  0,0,0,0,0,0,0,0,
                                  0,0,0,0,0,0,0,0,
                                  0,0,0,0,0,0,0,0,
                                  0,0,0,0,0,0,0,0,
                                  0,0,0,0,0,0,0,0,
                                  0,0,0,0,0,0,0,0,
                                  0,0,0,0,0,0,0,0};
                                                        
Of course you have to re-compile your code and upload it to the Arduino DUE for the new defaults to become effective.

### Using the settings files

The APC will create the above mentioned settings files when you use the settings menu to change the settings from the defaults. That means you can use a binary editor to change the values in the files on the SD card without having to change and re-compile your code.

Most sound packages do also contain the settings files to make this game work. So if your game is listed in the [available sounds](https://github.com/AmokSolderer/APC/blob/master/DOC/PinMame.md) list, you just need to copy the files to your SD card.

### Using the debug mode

If you have problems browsing the settings, you might want to use the [debug mode](https://github.com/AmokSolderer/APC/blob/master/DOC/Problems.md#the-debug-mode) to be able to see the settings menu in full text.  
You may use the defaults or settings file to activate the debug mode (as described above).

## Using the settings menu

To enter the APC settings you have to press the Advance button at the coin door with the Up/Down switch in 'up' position. If you're in Remote Control mode you have to keep it pressed for more than 1s.

After that you have to select whether you want to enter the system or game settings.

* The System Settings are valid for all selected active games
* The Game Settings are game specific. They change depending on which 'Active Game' is selected in the System Settings. This is not identical to the game you might want to run in PinMame, but you have to set your 'Active Game' to [Remote Control mode](https://github.com/AmokSolderer/APC/blob/master/DOC/RunGame.md#pinmame) in order to run PinMame.

Games with a credit display show 00 for System Settings and 01 for Game Settings in the left two digits. The number of the setting currently being shown appears in the right two digits of the credit display. This is important for pre System11 displays as they can show only numbers and no menu text. 

For pre Sys11 displays all text settings are represented by their item number as shown in the tables. For example, if a pre Sys11 display is selected and the credit display shows 00 01 you have selected the System Settings and the 'Active Game' setting is currently being shown. An early System11 display (upper display row alphanumerical and lower row numerical) will still try to show the name of the currently selected game as a text which is not perfect, but good enough. A pre System11 display will show the item number instead and if there is a 3 stated in the player 4 display then you're in Remote Control mode.

In settings mode use Advance to select the setting and the Game Start button to change it's value. If the Up/Down button is in down position then you're moving backwards.

If an SD card is present the settings are stored when you choose 'Exit Settings'.

## Using PinMame settings

While you're running PinMame you can adjust the original Williams System 4 - 11 adjustments as usual with one exception:  
You must not keep Advance pressed for more than 1 second with Up/Down in up position as this will trigger the APC settings. If you want to browse the Williams Settings quickly, just do it backwards with Up/Down in down position.

### System 3 game adjustments

Doing game adjustments on a System 3 game is done with DIP switches. The procedure is quite cumbersome and error prone which is why we're using the APC's settings menu instead.  
The following description works only for System 3 games being controlled by Lisy/PinMame, for all other generations the adjustment process hasn't changed from the original.

Keep the Advance switch pressed for more than one second with the Up/Down switch in up position. This will end PinMame and enter the settings menu of the APC. The content of the 18 System 3 adjustments is now stored in the 'Game Settings' 46 to 63 as shown in the table below (Game Settings in Remote Control mode).  
Enter the game settings and do your changes. When you're done, just select menu entry 65 (Exit Settings) and press the start button. After a few seconds PinMame will restart with the new settings applied.

## System Settings

| Number | Text  | Item Nr | Item Text | Default | Comment |
|--|--|--|--|--|--|
| 0 | Display Type | 0 | 4 Alpha+Credit | X | 4x 7 digit alphanumeric + credit |
| 0 |  | 1 | Sys11 Pinbot | - | 2x 7 digit alphanumeric + 2x 7 digit numeric + credit |
| 0 |  | 2 | Sys11 F-14 | - | 2x 7 digit alphanumeric + 2x 7 digit numeric |
| 0 |  | 3 | Sys11 BK2K | - | 2x 16 digit alphanumeric (inverted segments)|
| 0 |  | 4 | Sys11 Taxi | - | 2x 16 digit alphanumeric + 1x 7 digit numeric (non inverted segments)|
| 0 |  | 5 | Sys11 Riverboat | - | 2x 16 digit alphanumeric + 2x 7 digit numeric (inverted segments)|
| 0 |  | 6 | Data East 2x16 | - | 2x 16 digit alphanumeric (non inverted segments)|
| 0 |  | 7 | 7 | - | 4x 6 digit numeric + credit (System 3 - 6)|
| 0 |  | 8 | 8 | - | 4x 7 digit numeric + credit (System 7 + 9)|
| 1 | Active Game | 0 | Base Code | - | The very basics of a game SW |
| 1 |  | 1 | Black Knight | - | My own Black Knight game SW |
| 1 |  | 2 | Pinbot | - | My own Pinbot game SW |
| 1 |  | 3 | Remote Control | X | For controlling the APC remotely via USB or an onboard Raspberry Pi|
| 1 |  | 4 | Tutorial | - | The corresponding game SW to the game code tutorial Wiki|
| 2 | No of balls | - | - | 3 | Numerical setting - range 1 -5 |
| 3 | Free game | - | - | Yes | Bool setting |
| 4 | Connect Type | 0| Off | - | No remote control during Remote Control mode |
| 4 |  | 1 | On board | - | APC is controlled by the Pi on board |
| 4 |  | 2 | USB | X | APC is controlled via USB |
| 5 | Dim inserts | - | - | No | Bool setting - brightness of playfield lamps is set to 50% when on |
| 6 | Speaker volume | - | - | 0 | Numerical setting - range 1 - 255 / must be set to 0 when volume pot is connected at 10J4 / 1J16 |
| 7 | LED lamps | 0 | No LEDs | X | The APC_LED_exp board is not used |
| 7 |  | 1 | Additional | - | The APC_LED_exp board is used for the lamps 65+ |
| 7 |  | 2 | Playfld only | - | The APC_LED_exp board is only used for the lamps 9 - 64 |
| 7 |  | 3 | PlayfldBackbox | - | The APC_LED_exp board is used for the lamps 1 - 64 |
| 8 | No of LEDs | - | - | 64 | Numerical setting - range 1 - 192 / The length of the LED stripe. Setting is only effective when 'Additional' is selected as 'LED lamps' setting|
| 9 | Sol Exp Board | - | - | No | Bool setting - will use the solenoid expander board for solenoids 26 - 33 if set
| 10 | Debug Mode | 0 | Off | X | APC debug mode disabled |
| 10 |  | 1 | USB on | - | The number of active timers is shown in the credit display, game will stop on error and communication is active for the USB programming port |
| 10 |  | 2 | USB log | - | USB debug log is active |
| 11 | Backbox Lamps | 0| Column 1 | X | Backbox lamps are in lamp column 1 |
| 11 |  | 1 | Column 8 | - | Backbox lamps are in lamp column 8 |
| 11 |  | 2 | None | - | game has no controlled backbox lamps |
| 12 | Connect Startup | - | - | No | Bool setting - If active, then the connection type is not set by setting 4 (Connect Type) but by the state of the Up/Down switch during startup (and when leaving the settings). Switch in Up state selects the onboard Pi, otherwise the USB programming port |
| 13 | Restore Default | - | - | - | No setting - restores the default settings |
| 14 | Exit Settings | - | - | - | No setting - exits the settings mode and writes the new setting to an SD card if present |

## Game Settings in Remote Control mode

These game settings are only visible if 'Remote Control' is selected as the 'Active Game' in the 'System Settings'.

| Number | Text  | Item Nr | Item Text | Default | Comment |
|--|--|--|--|--|--|
| 0 | USB watchdog | - | - | No | Bool settings - disables all solenoids when no watchdog reset command is received for 1s |
| 1 | Debug Mode | 0 | Off | X | No debugging |
| 1 |  | 1 | USB | - | Shows the received commands in the displays |
| 1 |  | 2 | Audio | - | Audio debug mode for PinMame Sounds |
| 2 | PinMame Sound | 0 | APC | X | PinMame sounds are played on the APC sound HW |
| 2 | | 1 | Board | - | PinMame sounds are played on an external audio board |
| 3 | PinMame game | - | - | 0 | Numerical setting - [PinMame game number](https://github.com/AmokSolderer/APC/blob/master/DOC/lisyminigames.csv) |
| 4 | Lisy Debug | - | - | 0 | Numerical setting according to the [Controlling Lisy](https://github.com/AmokSolderer/APC/blob/master/DOC/LisyDebug.md) page |
| 5 | Ball Saver | 0 | Off | X | The optional ball saver is not active |
| 5 |  | 1 | On | - | The ball saver is active for all drained balls |
| 6 | Ball Saver Time | - | - | 20 | Numerical setting - range 5 - 250 / Active time of the Ball Saver |
| 7 | BG Music | 0 | PinMame default | X | Normal BG music |
| 7 |  | 1 | Music snd | - | Uses the MUSIC.SND file as BG music |
| 8 | Recycle Sol 1 | - | - | 0 | Numerical setting - Sets a recycle time of 250ms for the selected solenoid. Useful e.g. for slingshots to prevent machine gunning |
| 9 | Recycle Sol 2 | - | - | 0 | Same as above |
| 10| Recycle Sol 3 | - | - | 0 | Same as above |
| 11| Recycle Sol 4 | - | - | 0 | Same as above |
| 12- 45 | Setting Unused | - | – | - | They behave like boolean settings, but they have no effect |
| 46 | System3 Set 1 | - | - | - | Use this to change the 1st setting of system 3 games |
| 47 | System3 Set 2 | - | - | - | Use this to change the 2nd setting of system 3 games |
| 48 | System3 Set 3 | - | - | - | Use this to change the 3rd setting of system 3 games |
| 49 | System3 Set 4 | - | - | - | Use this to change the 4th setting of system 3 games |
| 50 | System3 Set 5 | - | - | - | Use this to change the 5th setting of system 3 games |
| 51 | System3 Set 6 | - | - | - | Use this to change the 6th setting of system 3 games |
| 52 | System3 Set 7 | - | - | - | Use this to change the 7th setting of system 3 games |
| 53 | System3 Set 8 | - | - | - | Use this to change the 8th setting of system 3 games |
| 54 | System3 Set 9 | - | - | - | Use this to change the 9th setting of system 3 games |
| 55 | System3 Set 10 | - | - | - | Use this to change the 10th setting of system 3 games |
| 56 | System3 Set 11 | - | - | - | Use this to change the 11th setting of system 3 games |
| 57 | System3 Set 12 | - | - | - | Use this to change the 12th setting of system 3 games |
| 58 | System3 Set 13 | - | - | - | Use this to change the 13th setting of system 3 games |
| 59 | System3 Set 14 | - | - | - | Use this to change the 14th setting of system 3 games |
| 60 | System3 Set 15 | - | - | - | Use this to change the 15th setting of system 3 games |
| 61 | System3 Set 16 | - | - | - | Use this to change the 16th setting of system 3 games |
| 62 | System3 Set 17 | - | - | - | Use this to change the 17th setting of system 3 games |
| 63 | System3 Set 18 | - | - | - | Use this to change the 18th setting of system 3 games |
| 64 | Restore Default | - | - | - | No setting - restores the default settings |
| 65 | Exit Settings | - | - | - | No setting - exits the settings mode and writes the new setting to an SD card if present |

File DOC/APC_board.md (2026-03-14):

# The APC board

First you should know what you're dealing with, so take a look at the [APC schematics](https://github.com/AmokSolderer/APC/blob/master/DOC/Hardware/APC_schematics.pdf). I have tried to design the hardware simple and straightforward, that means with a bit of hardware knowledge it shouldn't be a problem for you to understand how it works.

In the schematics the names of the connectors are given for System7 and System11, but the System7 names are also valid for System3 - 6 and the System11 names match to System9. The following picture should help you to determine where the various connectors belong. The direction of the Molex connectors is printed on the boards and also visible in the picture below: the friction lock belongs to the side where the additional thin line is drawn.  
The solenoid GND connector of Sys11 games (1J13) has only 4 pins, in the picture it is marked as a black rectangle. The X symbols indicate which pins have to be removed.

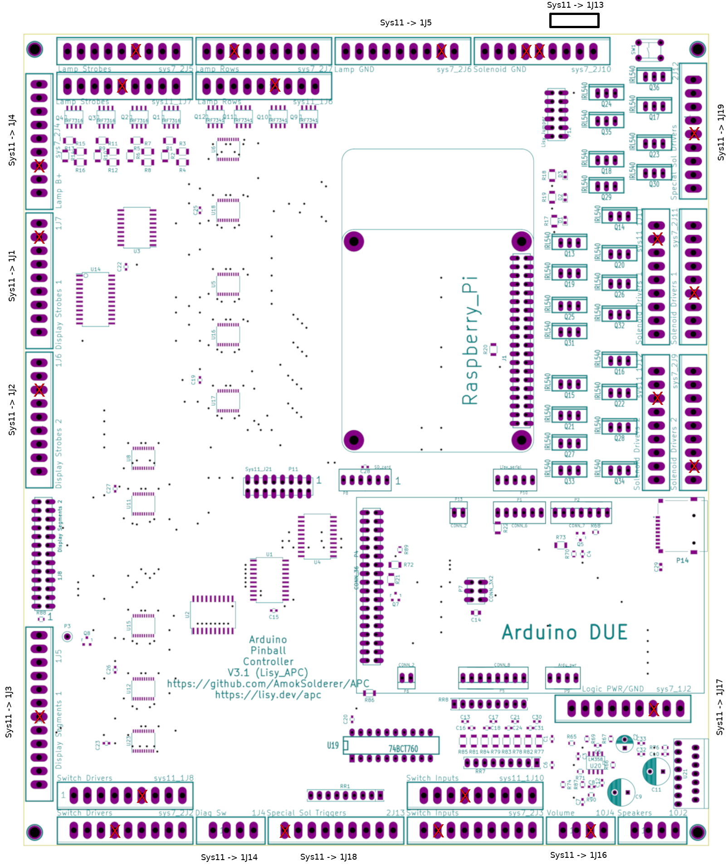
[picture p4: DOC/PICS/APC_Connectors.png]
APC connectors


However, the APC is only suited for you if you have some basic knowledge of electronics, because you can easily damage your precious pinball machine when you don't do things right.

## Order a board

I recommend to use [JLCPCB](https://jlcpcb.com) as your board manufacturer, because the assembly files are tailored to their specifications. You need to order at least five boards, so you might want to ask in the forum first whether someone from your country has a board for sale.  
If you want to place an order, the manufacturer will need the APC_Gerber.zip file to build the boards. You also have to select 'PCB Assembly' and choose the top side for assembly. In the next step you have to provide the APC_BOM.csv and APC_cpl_top.csv files to make them populate the parts. All required files are located [here](https://github.com/AmokSolderer/APC/tree/master/DOC/Hardware/APC_FabricationFiles_SOIC).

However, it has become increasingly difficult to get all the required parts. In this case JLCPCB would state an 'Inventory shortage' in the parts list. You can either try to select another part with the same package or you could pre-order the part. Go to the 'Parts Manager' to do so. If the pre-ordering was successful you can use these parts for your boards.

Note that JLCPCB will populate the Molex connectors, but they wont remove the key pins. This can be done easiliy by heating them up with a soldering iron and pulling them out with a pair of pliers.

## The Components

Most of the components can be populated by the board manufacturer. They can do all SMD and most of the other stuff as well. Hence, there're only a few components left for you to assemble. You can find a list of these components with their respective order number from [Mouser](http://www.mouser.com) and [Reichelt](http://www.reichelt.de) in the [Bill of Materials](https://github.com/AmokSolderer/APC/blob/master/DOC/Hardware/Assembly/APC_BOMselfSolder.pdf)

The german electronics retailer Reichelt doesn't sell all required components, but some (especially connectors) are much cheaper compared to Mouser, so for people in Europe it might still make sense to order them separately.

### TDA7496 availability

I got a notification from Mouser that the TDA7496 audio amplifier IC won't be produced any longer.

You can use the TDA7495 instead which is a pin compatible replacement. It's also discontinued, but at the moment the TDA7495 is available on eBay for a reasonable price. In China there are still large quantities of both ICs available for very low prices.
However, this might change in the future so you should be sure to get these ICs before you order any boards.

## The assembly

As the boards have the component names printed at the corresponding locations, you can just use the [Bill of Materials](https://github.com/AmokSolderer/APC/blob/master/DOC/Hardware/Assembly/APC_BOMselfSolder.pdf) to identify the  right component to put there.  
The resistor network RR8 has to be populated in the correct orientation. There's a marking for pin 1 printed on the APC boards. On the resistor networks pin 1 is usually marked with a dot.

## Getting your board started

Plug the Arduino DUE on your APC board, but don't populate the Pi yet. I recommend to do the basic tests before assembling the Pi.
The next step is to [Upload the SW](https://github.com/AmokSolderer/APC/blob/master/DOC/Upload_SW.md). I'd do this before you put the APC board into your pinball machine, because if this works you know, that your 5V supply has no short and is working properly.

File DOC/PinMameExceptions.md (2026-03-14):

# PinMameExceptions

The APC features a machine specific exception handling, which means that you can manipulate your game even though it is running in PinMame. To enable this for your machine you have to add a game specific section to the PinMameExceptions.ino file and recompile the SW.
You can manipulate sound, lamp, switch, display and solenoid commands. Some exceptions are mandatory to make the APC generate the sound for your machine correctly. A description for this is on the [PinMame sound howto](https://github.com/AmokSolderer/APC/blob/master/DOC/PinMame.md) page.

In this section we'll focus on exceptions that change a game. This can be just to fix flaws in the original game SW (or PinMame) or add new features.

## How it works

PinMame controls the APC by sending commands over the serial interface. Each of these commands triggers the APC SW to fullfill a specific task, e.g. turning on a lamp, report the latest activated switch and so on. Normally the APC does exactly what it has been told to do, but you can use the [APC SW framework](https://github.com/AmokSolderer/APC/blob/master/DOC/Software/APC_SW_reference.pdf) to program game specific exceptions which are collected in the file PinMameExceptions.ino.  

### Adding exceptions for your machine

Let's use the System 3 Disco Fever as an example how to use exception handling in practice:

First of all we need to generate a Disco Fever specific code section to handle all the required exceptions. There's a template named

    byte EX_Blank(byte Type, byte Command)

in PinMameExceptions.ino you could use as a start. So let's create a copy of this and rename it to

    byte EX_DiscoFever(byte Type, byte Command)

In order for the system to use this code section, we have to add it to EX_Init which is at the end of PinMameExceptions.ino and determines which code is used for which machine. For simplicity, the following code shows an EX_Init with only two machine entries and the default handler. In the real EX_Init the list is already much longer:

    void EX_Init(byte GameNumber) {
      switch(GameNumber) {
      case 4:                                             // Disco Fever
        PinMameException = EX_DiscoFever;                 // use exception rules for Flash
        break;
      case 6:                                             // Flash
        PinMameException = EX_Flash;                      // use exception rules for Flash
        break;
      default:
        PinMameException = EX_DummyProcess;}}
    
Each entry consists of a case statement with the [PinMame game number](https://github.com/AmokSolderer/APC/blob/master/DOC/lisyminigames.csv) as an argument. You can define all kind of optional stuff in these case statements, but the definition of the PinMameException is mandatory as it tells the system which code to use for this machine.  
All other games do not have an exception handler yet, so the exception pointer just points to a dummy process which provides some basic sound handling.

In order to implement some exceptions for Disco Fever, we can use our new 

    byte EX_DiscoFever(byte Type, byte Command){
      switch(Type){

The Type argument determines what kind of event should be dealt with. You can find a list of possible events at the top of PinMameExceptions.ino:

    #define SoundCommandCh1 0
    #define SoundCommandCh2 1
    #define SwitchActCommand 2
    #define SwitchRelCommand 3
    #define SolenoidActCommand 4
    #define SolenoidRelCommand 5
    #define LampOnCommand 6
    #define LampOffCommand 7
    #define WriteToDisplay0 8
    #define WriteToDisplay1 9
    #define WriteToDisplay2 10
    #define WriteToDisplay3 11
    #define WriteToDisplay4 12

The Command argument determines which specific lamp, solenoid, switch or sound shall be affected.  
For example

    case LampOnCommand:
      if (Command == 32) {
        TurnOnLamp(33);
        return(1);}

will turn on lamp 33 when PinMame requests lamp 32 to be turned on.  
The argument of the return command is important as it determines whether PinMame's original request will still be executed or not. In this case return(1) means that the original request will be ignored, so lamp 33 will be turned on INSTEAD of lamp 32. With return(0) lamp 32 would be turned on additionally to lamp 33.

Below are some more examples starting with the Disco Fever.

## Fixing the drop targets of pre System 7 games

PinMame has a timing issue with System 3,4 and 6 games. For some reason the activation times of some solenoids is too short to trigger them correctly. This is especially problematic with drop targets because they won't reset any more.  
Even though it's a PinMame issue we decided to fix this in PinMameExceptions which means you have to do it if your machines shows this problem.

This section shows the necessary code for the Disco Fever. In this machine solenoid 2 is for resetting the drop targets.  
Normally PinMame sends turn-on and off commands for the solenoids and does therefore control the activation time by itself. In order to increase the length of the activation time, we capture the turn-on command from PinMame and activate the solenoid for a time of our choosing, in this case 80ms.

    case SolenoidActCommand:
      if (Command == 2) {                               // ball release
        ActivateSolenoid(80, 2);                        // FEV drop target reset
        return(1);}

Here it's important to end this case with return(1) as the 1 will cause the APC not to process this command any further, which means it will skip the normal turn-on command for this solenoid.  
However, this alone won't do the trick. PinMame will still send the turn-off command for solenoid 2 which will turn it off even though the activation of 80ms time is not over yet. To prevent this from happening we have to tell the APC to ignore all solenoid turn-off commands for solenoid 2:

    case SolenoidRelCommand:
      if (Command == 2) {                               // ignore turn-off command 
        return(1);} 

We just use return(1) again to tell the APC not no process this command any further.

The complete PinMameExceptions to increase the activation times of both drop target reset coils look like this:

    byte EX_DiscoFever(byte Type, byte Command){
      switch(Type){
      case SolenoidActCommand:
        if (Command == 2) {                               // ball release
          ActivateSolenoid(80, 2);                        // FEV drop target reset
          return(1);}
        else if (Command == 3) {                          // ER drop target reset
          ActivateSolenoid(60, 3);                        // Fix to increase the strength of the ball release
          return(1);}
        return(0);
      case SolenoidRelCommand:
        if (Command == 2 || Command == 3) {               // ignore turn-off commands for drop target solenoids 
          return(1);}                                     // ignore it
        return(0);
      default:
        return(0);}}

## Doing exceptions for the magna save of the Jungle Lord

Jungle Lord features timed magna saves which means that the magnets are just activated for as long as the magna save buttons are pressed.
If we let PinMame handle this, then the message of the pressed button is forwarded from the APC to PinMame who will calculate an answer and in return send a command to turn on the magna save coil. Even though the reaction times are quite short it still feels a little sluggish sometimes and we want the APC to handle this directly.

As the whole process is triggered by the magna save button, the SwitchActCommand case is the right place to add our code:

    case SwitchActCommand:                              // activated switches
      if (Command == 49) {                              // right magnet button
        if (QueryLamp(8) && QueryLamp(2)) {             // right magnet and ball in play lamp lit?
          ActivateSolenoid(0, 22);}}                    // activate right magnet
      else if (Command == 50) {                         // left magnet button
        if (QueryLamp(39) && QueryLamp(2)) {            // left magnet and ball in play lamp lit?
          ActivateSolenoid(0, 21);}}                    // activate leftmagnet
      return(0);                                        // all switches are reported to PinMame

If the right magna save button is pressed, we check whether lamp 8 is lit which means that the player has activated the magna save feature. We also check for the 'Ball in Play' lamp 2 to prevent the magnet from being activated without a game running. If these conditions are met, the magna save coil 22 is activated.
The left magna save is treated accordingly.

The return value is important for all exceptions which do not affect the sound, because it determines whether the main program additionally tries to process this command afterwards (return(0)) or whether it just omitts any further processing. In our case returning a 1 would mean that we wouldn't tell PinMame about the magnet button being activated which would make no sense as PinMame has to count the seconds the magna save is on and turn off the magna save lamps if the player has none left.

For timed magna saves we have to do the same for the magna save buttons being released, we just don't have to check for any lit lamps:

    case SwitchRelCommand:                              // deactivated switches
      if (Command == 49){                               // right magnet button
        ReleaseSolenoid(22);}                           // turn off right magnet
      else if (Command == 50) {                         // left magnet button
        ReleaseSolenoid(21);}                           // turn off left magnet
      return(0);                                        // all switches are reported to PinMame

## Improving the System7 ball release

The previous example was just to improve the emulation of a machine, which is necessary to make your game work correct with PinMame. However, you are not limited to this, but you can also use this to apply changes to a game.

As an example I want to fix one nasty problem that affected both of my System7 machines.
It didn't happen often but regularly that a ball ejected into the plunger lane bounced back from the side rail and into the trunk again. If it got back into the trunk completely the SW would recognize this and eject the ball again. But sometimes the ball didn't really get back into the trunk. Instead it got stuck above the shooter lane feeder and there wasn't much I could do about it except of opening the coin door and operating the feeder manually to push the ball into the shooter lane. I really wonder how these games survived in the pubs with a bug like this.

With the APC we can fix this.
There is a switch in the shooter lane, so all we have to do is start a timer when the solenoid of the shooter lane feeder is activated. If the shooter lane switch is triggered within 3 seconds, we know the ball has been ejected successfully and we can just kill the timer. But if the timer runs out, we know the ball is probably stuck and we just operate the feeder again.

How does this look in code? First we need a handling routine for our timer. As we're going to need this for most if not all System7 machines, I've generated a generic timer handler for our problem that can be used by all machines:

    void EX_BallRelease(byte State) {                     // repeat ball eject in case the ball got stuck
      static byte Timer;                                  // stores the timer number
      switch (State) {                                    // determines what to do
      case 0:                                             // kill the timer
        if (Timer) {                                      // if a timer is active
          KillTimer(Timer);                               // kill it
          Timer = 0;}                                     // and set Timer = 0 to indicate that no timer is active
        break;
      case 1:                                             // start a timer
        if (!Timer) {                                     // if no timer is active
          Timer = ActivateTimer(3000, 2, EX_BallRelease);}  // start one for 3s with 2 as the argument
        break;
      case 2:                                             // timer has run out
        ActivateSolenoid(40, EX_EjectSolenoid);           // activate the shooter lane feeder again
        Timer = ActivateTimer(3000, 2, EX_BallRelease);}} // and restart the timer

This routine shall be called with a State argument which determines what it has to do.
If State is 0 then the timer is not needed any more and must be deactivated. In our case this would happen if the ball has triggered the shooter lane switch.
State = 1 means that a timer shall be started. The number of this timer is being stored in the Timer variable and the Timer is configured to call our handler again after 3s. When it does so it'll pass a 2 as an argument which will indicate that our handling routine has been called by the timer.
Hence, our handler knows that the timer has run out when it's called with State = 2 which means that the ball is probably stuck. So it activates the shooter lane feeder again and restarts the timer in case the ball gets stuck again.
For more information about timers read the [APC SW reference](https://github.com/AmokSolderer/APC/blob/master/DOC/Software/APC_SW_reference.pdf) and the [Basic Game Functions](https://github.com/AmokSolderer/APC/blob/master/DOC/GameCodeTutorial.md#2-basic-game-functions) tutorial.

With this timer handler in place we just have to tell our exception handler to use it. First of all it needs to know which coil is for the shooter lane feeder. In case of the Jungle Lord this is solenoid number 2 which we already defined before in EX_Init by setting EX_EjectSolenoid = 2.
The rest is easy. We just have to create an exception for EX_EjectSolenoid being activated

    case SolenoidActCommand:                            // activated solenoids
      if (Command == EX_EjectSolenoid){                 // ball eject coil
        if (QueryLamp(2)) {                             // ball in play lamp lit?
          EX_BallRelease(1);}}                          // start ball release timer
      return(0);                                        // solenoid will be activated

If the shooter lane feeder is activated, we first check whether a game is running by probing the 'Ball in Play' lamp 2. This is because we don't want our fix to be accidentially triggered in test mode. If the conditions are met we call our timer handler EX_BallRelease with an argument of 1, as this will start a timer. Note that we return a value of 0 as we don't want to block the activation of this solenoid.
Last but not least we have to switch off the timer when the shooter lane switch (43) is triggered. This is done by calling EX_BallRelease with an argument of 0.

    case SwitchActCommand:                              // activated switches
      if (Command == 43) {                              // ball successfully ejected
        EX_BallRelease(0);}                             // stop ball release timer

These were just a few simple examples of what you could do with exception handling, but with this you could even do significant changes of the rules without having to program the whole game by yourself.

Refer to PinMameExceptions.ino to see all the above mentioned changes in place.
For more information about using the APC API read the [APC SW reference](https://github.com/AmokSolderer/APC/blob/master/DOC/Software/APC_SW_reference.pdf) and the [Basic Game Functions](https://github.com/AmokSolderer/APC/blob/master/DOC/GameCodeTutorial.md#2-basic-game-functions) tutorial.
Watch my [Jungle Lord video](https://www.youtube.com/watch?v=bbfhH_-gMfE) so see an example. The corresponding code can be found in PinMameExceptions.ino in the AmokPrivate branch on Github.

## How to add a ball saver

### The easy way

There's a general ball saver program included in PinMameExceptions.ino that can be used for most machines. The ball saver is controlled by the [game settings](https://github.com/AmokSolderer/APC/blob/master/DOC/Settings.md) number 5 and 6.

To enable the ball saver for your machine you have to provide the number of certain switches, lamps and solenoids.  
At the top of PinMameExceptions.ino there's a section where the ball saver related properties for various machines are already present. In EX_SpaceStationProperties all properties are decribed by line comments. Use this as an example to generate the properties for your machine.

    const byte EX_SpaceStationProperties[13] = {          // machine properties for ball saver
        10,                                               // number of the outhole switch
        11,                                               // number of the 1st trunk switch (active if one ball is in the trunk) - set to 0 if machine has only one ball (-> no trunk)
        12,                                               // number of the 2nd trunk switch (active if a second ball is in the trunk)
        13,                                               // number of the 3rd trunk switch (active if a third ball is in the trunk) - set to 0 if machine has only two balls
        0,                                                // number of the 4th trunk switch (active if a fourth ball is in the trunk) - set to 0 if machine has only three balls
        17,                                               // number of the left outlane switch
        32,                                               // number of the right outlane switch
        12,                                               // number of the AC relay solenoid (set to 0 if machine has no AC relay)
        13,                                               // number of the left kickback solenoid (set to 0 if machine has no left kickback)
        0,                                                // number of the right kickback solenoid (set to 0 if machine has no right kickback)
        1,                                                // number of the outhole kicker solenoid
        2,                                                // number of the shooter lane feeder solenoid (set to 0 if machine has no shooter lane feeder (only one ball)
        42};                                              // number of the extra ball lamp (on the playfield) which is supposed to blink when ball saver is active

After that you have to register your properties by setting the EX_Machine pointer accordingly. The best place to do this is in EX_Init where the PinMameExceptions of your machine have to be registered anyway. For Space Station this looks like below:

    case 48:                                            // Space Station
      PinMameException = EX_SpaceStation;               // use exception rules for Space Station
      EX_Machine = EX_SpaceStationProperties;           // machine properties for ball saver
      break;
    
As a last step you have to add the call for the ball saver to your PinMameExceptions. Note that the ball saver is called only when the USB_BallSave setting is active.

    if (game_settings[USB_BallSave]) {                  // ball saver set to active?
      if (EX_BallSaver(Type, Command)) {                // include ball saver
        return(1);}}                                    // omit command if ball saver says so
      
This should be done at the beginning of the exceptions so the ball saver can decide whether a command is processed by PinMame or skipped. 

    byte EX_SpaceStation(byte Type, byte Command){
      static byte LastMusic;
      if (game_settings[USB_BallSave]) {                  // ball saver set to active?
        if (EX_BallSaver(Type, Command)) {                // include ball saver
          return(1);}}                                    // omit command if ball saver says so
      switch(Type){

In this example you can see that the ball saver part should be added in front of the switch(Type) command.

### The hard way

Of course you can also program an individual ball saver tailored to your machine, but this can become quite complicated, especially if your machine has an AC relay and more than one ball.

My Comet has neither and it really needs an individual ball saver as it makes me really angry when it drowns my balls in the outlanes before I even had a chance to touch them with a flipper. My first countermeasure was to remove the plumb bob tilt. By this I could nudge the ball out of the left outlane back into play (this is due to the special left outlane of the Comet). But as I had an APC board installed I could do it in a more subtle way eventually. My [Comet video](https://youtu.be/JbgMa_pn0Lo) makes more clear what I mean.

The code for this ball saver is quite simple. These are the complete PinMameExceptions of my Comet:

    byte EX_Comet(byte Type, byte Command) {
      static byte LastSwitch;                             // stores the number of the last activated switch
      static byte BlindPinmame;                           // hide switches from PinMame while active
      static byte Timer = 0;
      switch(Type) {
      case SoundCommandCh1:                               // sound commands for channel 1
        if (!Command || Command > 253) {                  // sound command 0x00 and 0xff -> stop sound
          AfterMusic = 0;
          StopPlayingMusic();
          StopPlayingSound();}
        else if (Command == 11) { }                       // ignore sound command 0x0b
        else if (Command == 47) {                         // play BG music
          PlayMusic(50, "0_2f.snd");
          QueueNextMusic("0_2f.snd");}                    // track is looping so queue it also
        else {                                            // handle standard sound
          if (Command == 9) {
            MusicVolume = 4;}                             // reduce music volume
          if (Command == 241) {
            RestoreMusicVolumeAfterSound(25);}            // and restore it
          char FileName[9] = "0_00.snd";
          if (USB_GenerateFilename(1, Command, FileName)) { // create filename and check whether file is present
            PlaySound(51, (char*) FileName);}}
        return(0);                                        // no exception rule found for this type so proceed as normal
      case SwitchActCommand:                              // activated switches
        if (BlindPinmame) {                               // hide switches from PinMame
          if (Command == 31 || Command == 32 || Command == 44) {
            return(1);}                                   // hide these switches from PinMame
          if (Command == 45) {                            // outhole switch?
            if (Timer) {                                  // timer still running?
              KillTimer(Timer);                           // stop it
              Timer = 0;}
            ActivateSolenoid(40, 1);                      // kick ball into plunger lane
            RemoveBlinkLamp(60);                          // stop blinking the extra ball lamps
            RemoveBlinkLamp(5);
            if (BlindPinmame > 1) {                       // extra ball lamps were on before?
              TurnOnLamp(60);
              TurnOnLamp(5);}
            BlindPinmame = 0;                             // and don't fool PinMame any longer
            return(1);}}                                  // hide this switch from PinMame
        else {                                            // normal mode
          if ((Command == 44 && (game_settings[USB_Option1] & 2)) || (Command == 31 && (game_settings[USB_Option1] & 1))) { // Ball Saver for outlanes active?
            if ((LastSwitch > 32) && (LastSwitch < 43)) { // ball dropped from the bumpers directly into the outlane?
              if (QueryLamp(60)) {                        // extra ball lamp lit?
                BlindPinmame = 2;}
              else {                                      // extra ball lamp not lit
                BlindPinmame = 1;}
              AddBlinkLamp(60, 150);                      // blink extra ball lamps
              AddBlinkLamp(5, 150);
              Timer = ActivateTimer(5000, 1, EX_Comet2);  // wait 5s for the ball to reach the outhole
              return(1);}}                                // hide this switch from PinMame
          else {                                          // switches are reported normally
            LastSwitch = Command;}}
        return(0);
      case 50:                                            // timer of ball saver has run out
        Timer = 0;
        if (BlindPinmame) {                               // ball saver still active?
          RemoveBlinkLamp(60);                            // stop blinking the extra ball lamps
          RemoveBlinkLamp(5);
          if (BlindPinmame > 1) {                         // extra ball lamps were on before?
            TurnOnLamp(60);
            TurnOnLamp(5);}
          BlindPinmame = 0;}                              // and don't fool PinMame any longer
        return(0);
      default:
        return(0);}}                                      // switch will also be reported to PinMame.

    void EX_Comet2(byte Dummy) {                          // to be called by timer from EX_Comet
      UNUSED(Dummy);
      EX_Comet(50, 0);}

The first SoundCommandCh1 exceptions are necessary for the sound of the Comet to work properly and have nothing to do with ball saver which starts with the SwitchActCommand exception.

Normally the BlindPinmame variable is zero which means the ball saver is passive and all switches are reported to PinMame. All the exception does in this 'normal mode' is to store the number of each activated switch in the LastSwitch variable.
If switch 31 or 44 (outlanes) is triggered and the corresponding ball saver is activated in the settings, the LastSwitch variable is checked. If the last switch belongs to the bumper area (switches 32 - 43) the ball saver becomes active by blinking the extra ball lamps and changing the value of BlindPinmame to 1 or 2 depending on whether the extra ball lamp was on or off before. A return(1) means that the activation of the outlane switch is not reported to PinMame.
This is also valid for any subsequent activation of the outlane switches (31, 32, 44) as long as BlindPinmame is different from zero.
If Switch 45 is triggered (outhole) then solenoid 1 is activated (shooter lane feeder), the state of the extra ball lamps is restored and BlindPinmame is cleared to deactivate the ball saver.
This is basically enough, the old game SW might wonder why the ball suddenly pops up in the shooter lane, but who cares as long as the gameplay resumes normally.

However, due to the special left outlane design of the Comet, it is possible to bounce the ball from the outlane back into play. For our exception this would mean that BlindPinmame would be set when the outlane switch is triggered and would stay active until the ball finally reaches the outhole. As the ball has been bouncing back it didn't reach the outhole when it was meant to which means that the ball saver stays active until the next regular ball drain happens.
To prevent this from happening a timer is started when the ball saver is activated and if the ball doesn't reach the outhole within 5 seconds then it deactivates itself.

You can find this code in the PinMameExceptions of the AmokPrivate branch in GitHub.

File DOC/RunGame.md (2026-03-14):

# Run a game

So you've done the tests and you have the Base Code running. If you've also [adjusted the Base Code](https://github.com/AmokSolderer/APC/blob/master/DOC/SetUpBC.md) to your machine then you can already press the Game Start button and play a very basic game.

After you've had enough fun with the Base Code you have the following options:

* Use Lisy/PinMame to run the original game code on a Raspberry Pi
* Create your game in MPF and let it control the APC
* Do your own game code in C and use the APC SW framework

## PinMame

The APC by itself cannot run the original Williams EPROM software, but you can use PinMame to emulate the pinball's hardware. By this you can run the old game SW on the APC. The easiest way to do this is to plug a Raspberry Pi on the APC board and install Lisy on it.  
Here's what to do:

1. Enter the [System Settings](https://github.com/AmokSolderer/APC/blob/master/DOC/Settings.md#system-settings)  
1.1. Select 'Remote Control' as the Active Game  
1.2. Check that 'On Board' is selected in the 'Connect Type' setting  
2. Enter the [Game Settings of the Remote Control Mode](https://github.com/AmokSolderer/APC/blob/master/DOC/Settings.md#game-settings-in-remote-control-mode)  
2.1. Select the corresponding [PinMame game number](https://github.com/AmokSolderer/APC/blob/master/DOC/lisyminigames.csv) in the Game Settings  
2.2. If you want to let the APC generate the audio then the Game Setting 'PinMame Sound' has to be APC, 'Board' means that an old audio board is used which is possible for System 3 - 7 machines. System 7 machines need an additional cable for this to work  
2.3. Exit the settings and switch off your machine  
3. Go to the [Lisy project page](https://lisy.dev/apc.html) and download a Lisy image file. Note that only the Raspberry Pi Zero, Zero W, Pi 2W, 3A+, 3B+ as well as the Banana PI M2 Zero models are currently supported by Lisy.  
3.1. Install the image file on an SD card and put it in your Raspberry Pi  
3.2. Install the Pi on your APC board  
4. Turn on your pinball machine  
4.1. The 'Booting Lisy' message should appear in your displays  
4.2. After a while the yellow on board LED will be lit and the name of the selected game will appear in the displays as well as a countdown  
4.3. The green LED will be lit and the game should start

Most Williams games go into 'Factory Settings' mode when started for the first time. That means if the game doesn't start, use the Advance and Up/Down Buttons to navigate and quit the Williams settings. Note that as you're now in the original Williams settings you can navigate them as usual with one exception:  
You must not keep Advance pressed for more than 1 second with Up/Down in up position as this will trigger the APC settings. If you want to browse the Williams Settings quickly, just do it backwards with Up/Down in down position.

## PinMame sound

### Using old audio boards

For some game generations you could install the original audio board. In this case you cannot do any sound related changes of course.  
For System 3 - 6, the sound board is controlled by some reserved solenoid drivers, so it will work out of the box. System 7 needs an [adapter](https://github.com/AmokSolderer/APC/blob/master/DOC/Prepare.md#system-7-audio-cable) for connecting the audio board to the HW extension interface of the APC.  
For the APC to control the external audio board you have to enter the [game settings](https://github.com/AmokSolderer/APC/blob/master/DOC/Settings.md#game-settings-in-remote-control-mode) while in Remote Control Mode and set setting 2 (PinMame Sound) from 0 (APC) to 1 (Board).

System 9 and 11 audio boards are not supported, you have to let the APC generate the sound instead.

### Using the APC to generate audio

Letting the APC generate the sounds has several benefits.

The audio quality of the APC is quite good. It is also better in noise suppression than the old audio boards, so if you have a hum in your sound due to worn out capacitors, the chances are that it is much weaker with the APC.  
You can also change your sounds as you wish. This can be as simple as replacing certain sound files, but you could also add a music track to your old System 3 - 7 game. Let your Flash play Queen as background music if you like.

The drawback of this is that someone has to extract the music files from PinMame and if your game is not already supported then this someone is probably you.

Check the table on the [PinMame Sound](https://github.com/AmokSolderer/APC/blob/master/DOC/PinMame.md) page to see whether your game is already supported and the audio files are available. If your game is listet there, you can simply request the files and put them on the SD card on the APC board (not the one of the Pi). That's it, have fun.  
If your game is not yet supported then you should also read this page to find out how to proceed.

### Emulation speed

It might be that your game is not running at the correct speed, e.g. if your bonus sound is running out but your game is still counting. In this case you can change PinMame's emulation speed. To do this you have to remove the SD card from your Raspberry Pi and access the file  
boot/lisy/lisy_m/cfg/lisyminigames.csv  
There's a throttle value specified for each game, the default for most games is 120. Changing this value to a lower value will make the game run faster and vice versa.

## MPF

If you want to do your own rules without having to program in C, the [Mission Pinball Framework](http://missionpinball.org/) might be your method of choice. It can run on a PC which then controls the APC via USB. You'd have to select 'Remote Control' as the Active Game and  'Connect Type' to 'USB' in the [System Settings](https://github.com/AmokSolderer/APC/blob/master/DOC/Settings.md#system-settings).

Most of the switch numbering and so on is quite straightforward but there're some [APC specialties](https://github.com/AmokSolderer/APC/blob/master/DOC/Specialties.md) you should be aware of when doing your own game.

We can also let Lisy run MPF which would then work without a PC, but we'd do this only on request.

Here you can find my basic [MPF setup](https://github.com/AmokSolderer/APC/tree/master/DOC/Software/MPF)

## C code

If you're familiar with C you can also program the APC directly. This SW would then run on the Arduino itself with no need for an additional PC or Raspberry Pi.  
For this the APC software offers an [API](https://github.com/AmokSolderer/APC/blob/master/DOC/Software/APC_SW_reference.pdf) providing the necessary commands to control a pinball machine. It's still a lot of effort to program a game completely from scratch, but you could even run your game in PinMame and only use the API to do changes or extensions to the original rules.

The APC software itself consists of two parts: the operating system APC.ino and the game specific code. The former controls the hardware and offers an application interface (API) for the game specific software to use. For an overview of the available API variables and commands please take a look at the
[APC software reference](https://github.com/AmokSolderer/APC/blob/master/DOC/Software/APC_SW_reference.pdf).

I have written game codes for my Black Knight and Pinbot. They are still not final, but good enough to have fun with and to use as a reference when writing own code. Additionally there's a [Base Code](https://github.com/AmokSolderer/APC/blob/master/BaseCode.ino) which should serve as a starting point for you to do your own game. It contains the very basics of a pinball game and it can be easily adapted to your machine. As a startup guide how to start writing game code I have written a short [tutorial](https://github.com/AmokSolderer/APC/blob/master/DOC/GameCodeTutorial.md).

Most of the switch numbering and so on is quite straightforward but there're some [APC specialties](https://github.com/AmokSolderer/APC/blob/master/DOC/Specialties.md) you should be aware of when doing your own game.

Please note that I have equipped my Black Knight with a [special alphanumerical display](https://github.com/AmokSolderer/APC/blob/master/DOC/Sys7Alpha.md) for pre System11 machines and that advanced APC commands like scrolling are currently not usable with numerical only displays. This is because I think that these displays are not suited for homebrew machines. If you do all the work needed to do your own game code, you'd for sure want to have a display with letters, otherwise you wouldn't be able to even have a decent high score list. Additionally it would be quite cumbersome to debug some game software without the display being able to show letters. Therfore I recommend to use an early System11 display which has at least one row with alphanumeric displays (or build my [System7Alpha](https://github.com/AmokSolderer/APC/blob/master/DOC/Sys7Alpha.md)). However, the basic software support is implemented, which means you can use the old displays without any restrictions you just have to do a bit more coding to get all the features. And if you just want to use them with PinMame to replace your old boards these displays will work perfectly well.

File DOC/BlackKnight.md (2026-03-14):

# The APC Black Knight

This page is about the BlackKnight.ino game SW which is part of the APC SW. Note that you have to have the Black Knight sound files for this game to work.  
Some features like the High Score table are only available when my [4 Alpha+Credit](https://github.com/AmokSolderer/APC/blob/master/DOC/Sys7Alpha.md) display is used.

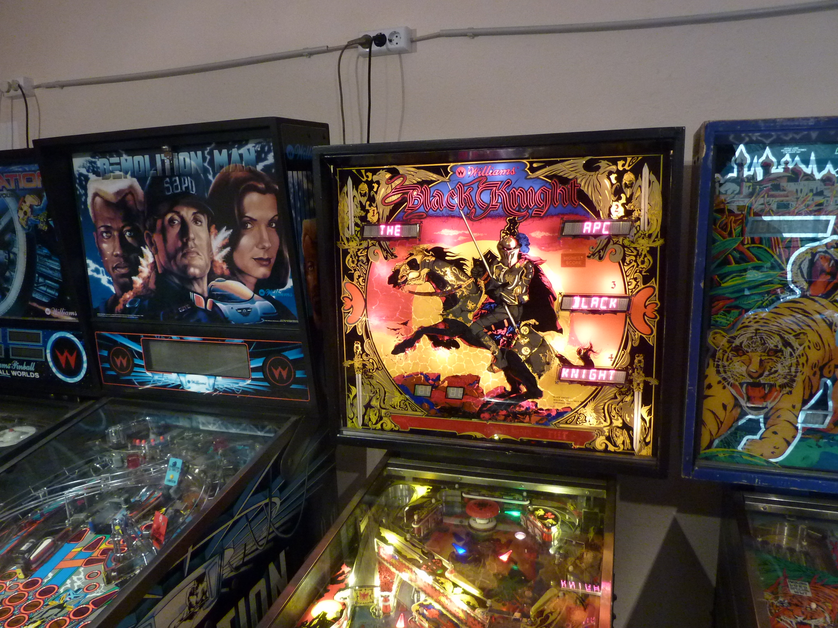
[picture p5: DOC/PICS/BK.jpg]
APC Black Knight


This is a view inside the backbox.

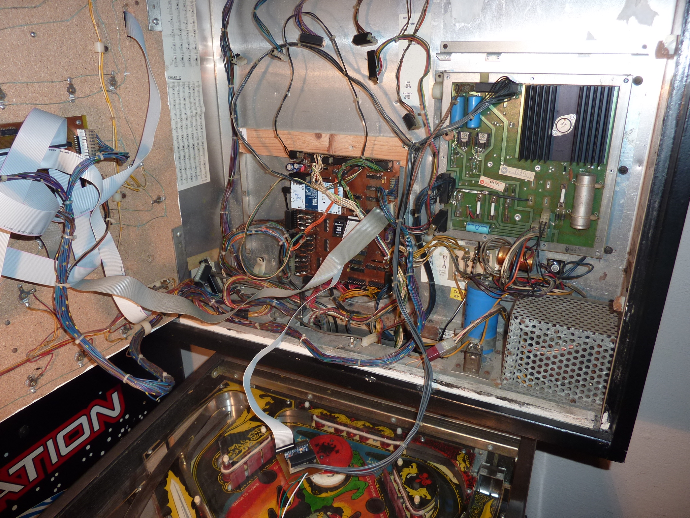
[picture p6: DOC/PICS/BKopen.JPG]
APC open BK


I'm using an APC 2 prototype board for this. As I'm running the code natively on the Arduino I don't need Lisy/PinMame and therefore no Raspberry Pi.

The LED_exp board which is connected here is also not needed.

## Features

* Timed Magna Saves -> When activated, the Magna Saves behave like in games like Jungle Lord, for the magnets are active as long as the corresponding button is being held and you still have Magna Save Time left. Clearing a drop target bank adds one second to the Magna Save Time. The Black Knight is lacking the playfield lamps to indicate the remaining Magna Save Time, so this is done by letting the Magna Save lamps blink. The slower the blinking frequency the more Magna Save Time is left until the lamps stay on permanently when the Magna Save Time has reached 5 seconds.
* Multi Ball Jackpot -> When activated a music score is played after Multiball has started. After all balls are released a music score starts and the lamp of the lower eject hole starts blinking. A shot to this hole enables the upper lock for Jackpot. After the Jackpot has been scored, the lower hole starts blinking and the Jackpot can be enabled again.
* Improved ball release -> In System7 games it sometimes happens that a ball ejected into the plunger lane bounces back from the side rail and into the trunk again. If it gets back into the trunk completely the SW will recognize this and eject the ball again. But sometimes the ball doesn't really get back into the trunk. Instead it gets stuck above the shooter lane feeder and there isn't much to do about it except of opening the coin door and operating the feeder manually to push the ball into the shooter lane. The APC Black Knight SW offers a settings to adjust the strength of the ball feeder. When properly adjusted this avoids that the ball is bouncing back.
* Ball search -> The SW features a ball search mode which is started when no playfield switch has been triggered for 30 seconds. The SW will recheck the locks and the ball through and will activate certain solenoids if a ball is missing.
* High Score table -> This feature is only available if '4 Alpha+Credit' is selected as the Display Type for it doesn't make much sense to enter initials no one is able to see. However, with the correct display installed you can enter you initials by using the Magna Save buttons. 

## How to set up this game

You need to have the audio files for this game. I have added the multiball music file to the Black Knight sound package. You can download it from the [PinMame Sound](https://github.com/AmokSolderer/APC/blob/master/DOC/PinMame.md) page.  

If you want to use the Multiball Jackpot feature you need to pick a music track to be played during Multi Ball. Take a track of your choice, convert it to the APC sound format and rename it to BK_M01.snd.  
The same needs to be done for the High Score table feature. In this case the name of the music track has to be BK_M02.snd. As already mentioned, the High Score table is only available when alphanumeric displays are used.

## BK Game Settings

| Number | Text  | Item Nr | Item Text | Default | Comment |
|--|--|--|--|--|--|
| 0 | Timed Magna | - | - | No | Bool setting - see features description |
| 1 | Replay Score | 0 | 1000000 | X | Set 1 million as replay score |
| 1 |  | 1 | 1500000 | - | Set 1.5 million as replay score |
| 1 |  | 2 | 2000000 | - | Set 2 million as replay score |
| 1 |  | 3 | 2500000 | - | Set 2.5 million as replay score |
| 2 | Multiball Jackpot | 0 | Off | X | Turn the multiball jackpot off |
| 2 |  | 1 | 500000 | - | Set 500K as multiball jackpot |
| 2 |  | 2 | 750000 | - | Set 750K as multiball jackpot |
| 2 |  | 3 | 1000000 | - | Set 1 million as multiball jackpot |
| 3 | Multiball volume | - | - | 0 | Numerical setting - range 0 - 30 / can be used to increase the volume during multiball. Does only work when the digital volume control of the APC is used and not the old volume pot |
| 4 | High Score volume | - | - | 0 | Numerical setting - range 0 - 30 / can be used to increase the volume during high score entry. Does only work when the digital volume control of the APC is used and not the old volume pot |
| 5 | Ball eject strength  | - | - | 30 | Numerical setting - range 0 - 30 / activation time of the ball ramp thrower (solenoid 6) in ms. Adjust this to avoid that the ball is bouncing back into the trunk|
| 6 | Ball Saver | 0 | Off | X | The optional ball saver is not active |
| 6 |  | 1 | On | - | The ball saver is active for all drained balls |
| 7 | Ball Saver Time | - | - | 20 | Numerical setting - range 5 - 250 / Active time of the Ball Saver |
| 8 | BG Music | 0 | default | X | Normal BG sounds |
| 8 |  | 1 | Music snd | - | Uses the MUSIC.SND file as BG music |
| 9 | Reset High | - | - | - | No setting - resets the high scores for this game |
| 10 | Restore Default | - | - | - | No setting - restores the default settings |
| 11 | Exit Settings | - | - | - | No setting - exits the settings mode and writes the new setting to an SD card if present |

Check the [settings page](https://github.com/AmokSolderer/APC/blob/master/DOC/Settings.md#using-the-settings-menu) if you're not sure how to use these game settings.

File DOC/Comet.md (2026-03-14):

# The APC Comet

The basic game runs in PinMame as described in the [PinMame Section](https://github.com/AmokSolderer/APC/blob/master/DOC/PinMame.md).  
This page is about the PinMameExtensions I did for my Comet. You need to install the SW from the AmokPrivate branch on GitHub to run my special extensions. 

As you can see, my Comet is using my [4 Alpha+Credit](https://github.com/AmokSolderer/APC/blob/master/DOC/Sys7Alpha.md) displays. All extensions will also work with the original numerical displays except the custom text feature of course.  
The blue shine on the playfield is from the LED effects I added to my GI.

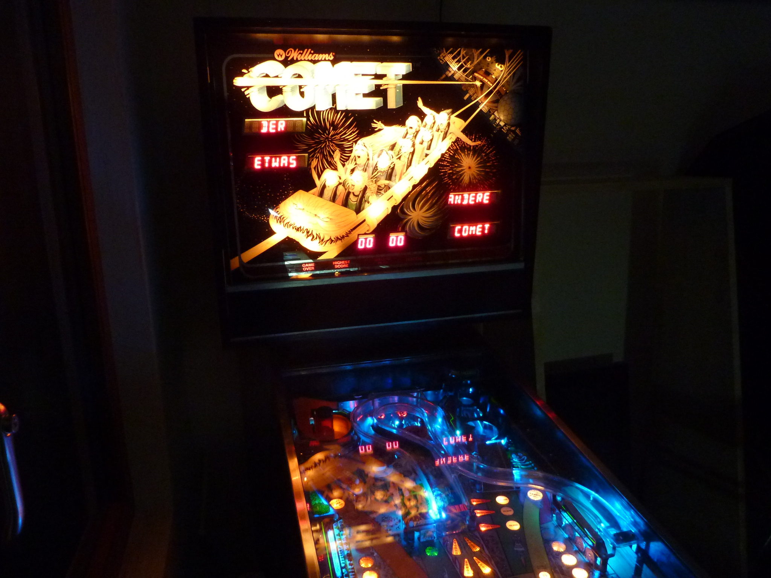
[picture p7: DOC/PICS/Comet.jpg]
APC Comet


This is a view inside the backbox.

APC open Comet

You can see the [LED expansion board](https://github.com/AmokSolderer/APC/blob/master/DOC/LEDexpBoard.md) which is needed for the LED effects.

## Features

* Ball saver -> Comet's outlanes are special. Alas, this leads to lots of balls falling from the bumper area into the left outlane without any way for the player to prevent this. Therefore I added an optional ball saver to my PinMameExtensions which gives back any ball which is lost through an outlane when the last active switch before was in the bumper area.  
Watch [this video](https://youtu.be/JbgMa_pn0Lo) to see how the ball saver works.
* LED GI -> I'm using the [LED expansion board](https://github.com/AmokSolderer/APC/blob/master/DOC/LEDexpBoard.md) with some RGB-LED chain instead of the old GI lightbulbs. You can choose your GI color in the Game Settings.
* GI gameplay animations -> During normal gameplay the GI LEDs behave like the normal GI, but in some occasions when the game shows some fireworks animation with the backbox flashers the GI does the same on the playfield, which makes this effect much stronger.
* GI attract animations -> I also use the GI LEDs to play some colorful animations every now and then during attract mode. There's a video showing my [GI LEDs](https://youtu.be/kLWVUdhSwfo) in action
* Custom Text Message -> As my game has alphanumeric displays I'm showing a custom text message when the GI LEDs are showing their animations during attract mode. The text is retrieved from the file Custom.txt which has to be present on the SD card.
* Custom game music -> Comet's original music is ... basic. So to hear a song of your choice during gameplay, name it MUSIC.SND, store it on the SD card and select 'Music bin' in the game settings.

## How to set up this game

* You need to have the audio files for this game. You can get the corresponding sound file package from the [PinMame Sound](https://github.com/AmokSolderer/APC/blob/master/DOC/PinMame.md) page
* Use the 'AmokPrivate' branch of GitHub to get the additional features. The normal 'master' branch just supports Comet without any special features.
* For the GI LED animations you need to install the necessary HW of course, but the other features work without it. The same applies for the alphanumeric displays.

## Comet Game Settings

| Number | Text  | Item Nr | Item Text | Default | Comment |
|--|--|--|--|--|--|
| 0 | USB watchdog | - | - | No | Bool setting - disables all solenoids when no watchdog reset command is received for 1s |
| 1 | Debug Mode | 0 | Off | X | No debugging |
| 1 |  | 1 | USB | - | Shows the received commands in the displays |
| 1 |  | 2 | Audio | - | Audio debug mode for PinMame Sounds |
| 2 | PinMame Sound | 0 | APC | X | PinMame sounds are played on the APC sound HW |
| 2 | | 1 | Board | - | PinMame sounds are played on an external audio board |
| 3 | PinMame game | - | - | 0 | Numerical setting - PinMame game number |
| 4 | Lisy Debug | - | - | 0 | Numerical setting according to the [Controlling Lisy](https://github.com/AmokSolderer/APC/blob/master/DOC/LisyDebug.md) page |
| 5 | Ball Saver | 0 | Off | X | No ball saver |
| 5 |  | 1 | Right Outlane | - | Ball saver only active for the right outlane |
| 5 |  | 2 | Left Outlane | - | Ball saver only active for the left outlane |
| 5 |  | 3 | Both Outlane | - | Ball saver active for both outlanes |
| 6 | LED GI red | - | - | 255 | Numerical setting (0-255) -> GI color setting red |
| 7 | LED GI green | - | - | 255 | Numerical setting (0-255) -> GI color setting green |
| 8 | LED GI blue | - | - | 255 | Numerical setting (0-255) -> GI color setting blue |
| 9 | BG Music | 0 | PinMame default | X | Normal Comet BG music |
| 9 |  | 1 | Music snd | - | Uses the MUSIC.snd file as BG music |
| 10 | Custom Text | - | - | No | Bool setting - Shows the custom text sometimes during attract mode |
| 11 | Restore Default | - | - | - | No setting - restores the default settings |
| 12 | Exit Settings | - | - | - | No setting - exits the settings mode and writes the new setting to an SD card if present |

## GI LEDs

These are the GI LEDs I've used. They match exactly into the holes for the normal lightbulbs.

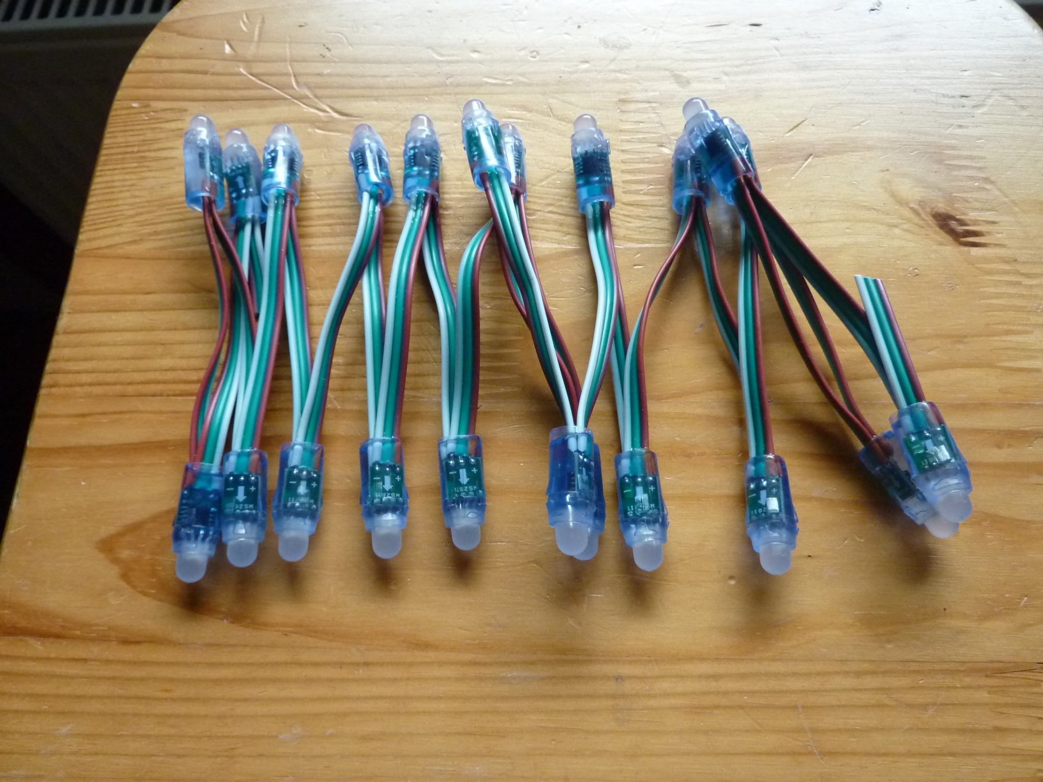
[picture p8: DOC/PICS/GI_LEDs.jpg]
GI_LEDs


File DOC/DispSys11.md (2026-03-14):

# LED displays for System11

This is an LED display set for early System 11 machines.

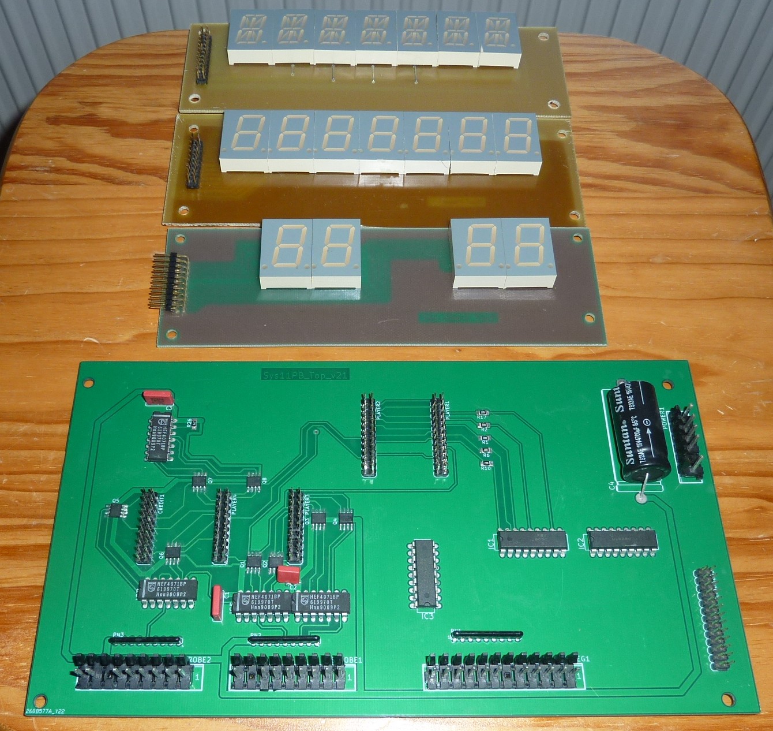
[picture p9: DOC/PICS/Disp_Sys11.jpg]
Disp_Sys11


It consists of 2 player boards with 7-digit alphanumerical player displays, 2 player boards with 7-digit numerical player displays, a credit board with 4 numerical LED elements and a driver board which contains the electronic circuits.  
I'm using this set only with red LED displays. They're very bright and shiny red.

The Gerber files, BOM and schematics of the driver board can be found [here](https://github.com/AmokSolderer/APC/tree/master/DOC/Hardware/Sys11_Display).  
The display boards are the same as in the normal System 7 LED display and the System 7 alphanumeric version.

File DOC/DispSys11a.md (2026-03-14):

# LED displays for System11a

This is an LED display set for System 11a and early 11b machines.

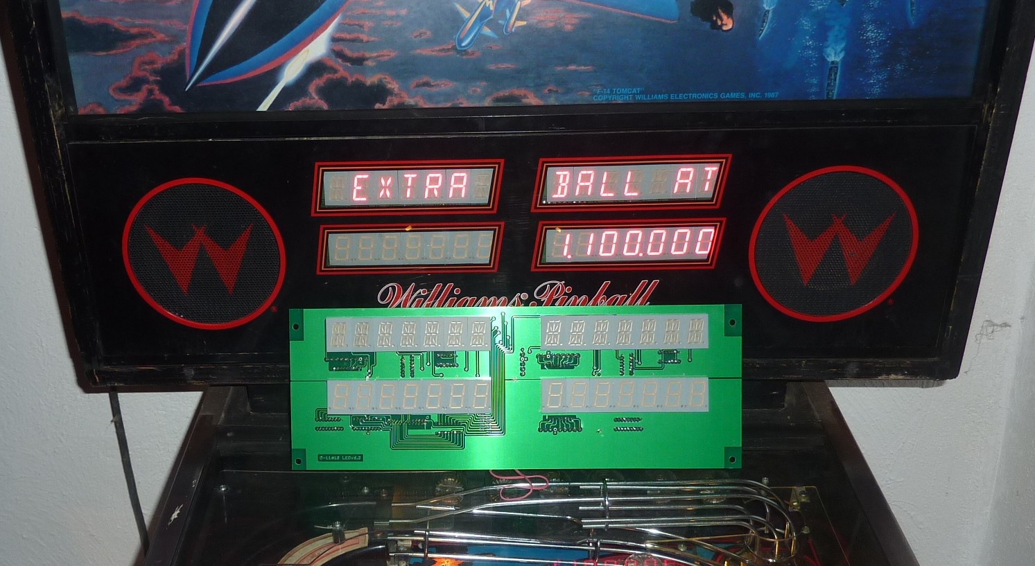
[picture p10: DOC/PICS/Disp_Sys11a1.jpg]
Disp_Sys11a1


It contains two 7-digit alphanumerical player displays, two 7-digit numerical player displays the electronic circuits to drive them.  
I'm using this set only with red LED displays. They're very bright and shiny red, unfortunately none of this shows well in the picture (the flash didn't help of course).

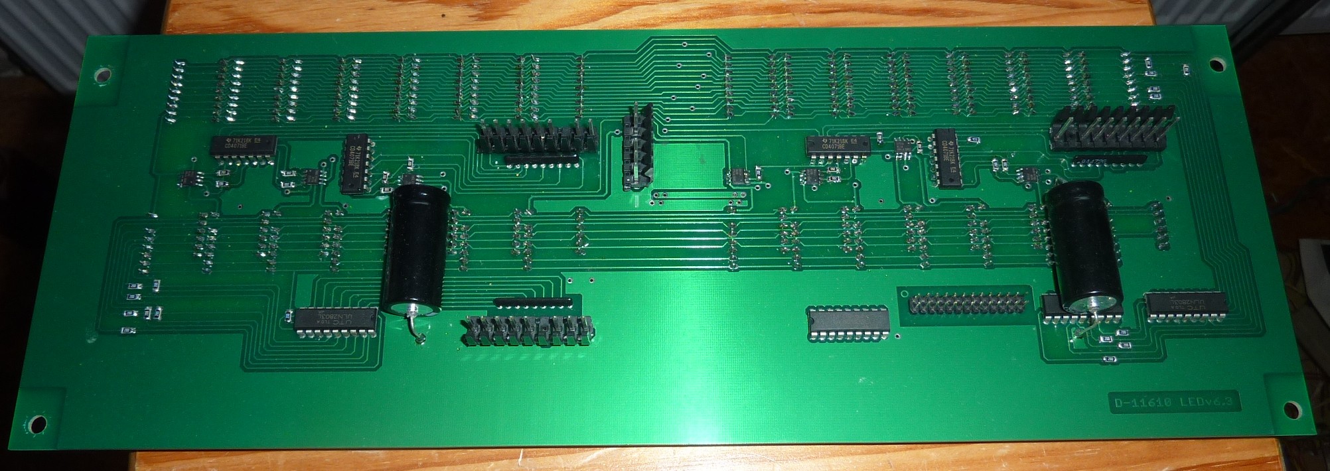
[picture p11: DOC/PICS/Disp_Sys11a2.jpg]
Disp_Sys11a2


The Gerber files, BOM and schematics can be found [here](https://github.com/AmokSolderer/APC/tree/master/DOC/Hardware/Sys11a_Display).

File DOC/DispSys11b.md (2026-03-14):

# LED displays for System11b

This is an LED display set for later System 11b and 11c machines.

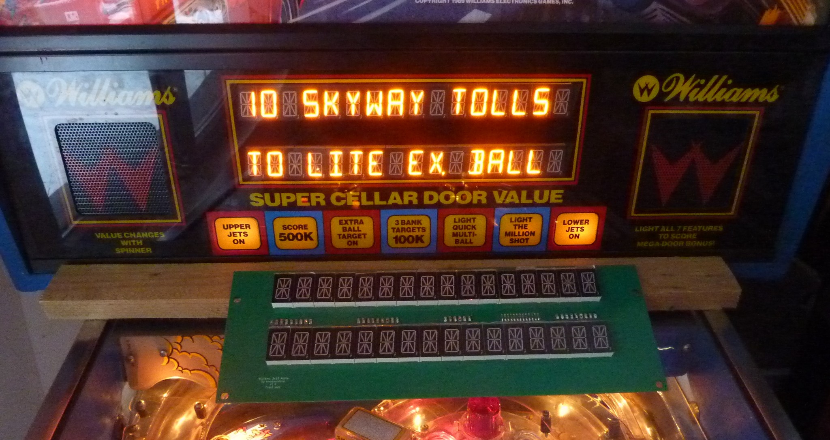
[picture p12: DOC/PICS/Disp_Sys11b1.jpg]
Disp_Sys11b1


It contains two 16-digit alphanumerical player displaysand the electronic circuits to drive them.  
I'm using this set with amber LED displays. The color is very close to the original, but they're brighter.
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

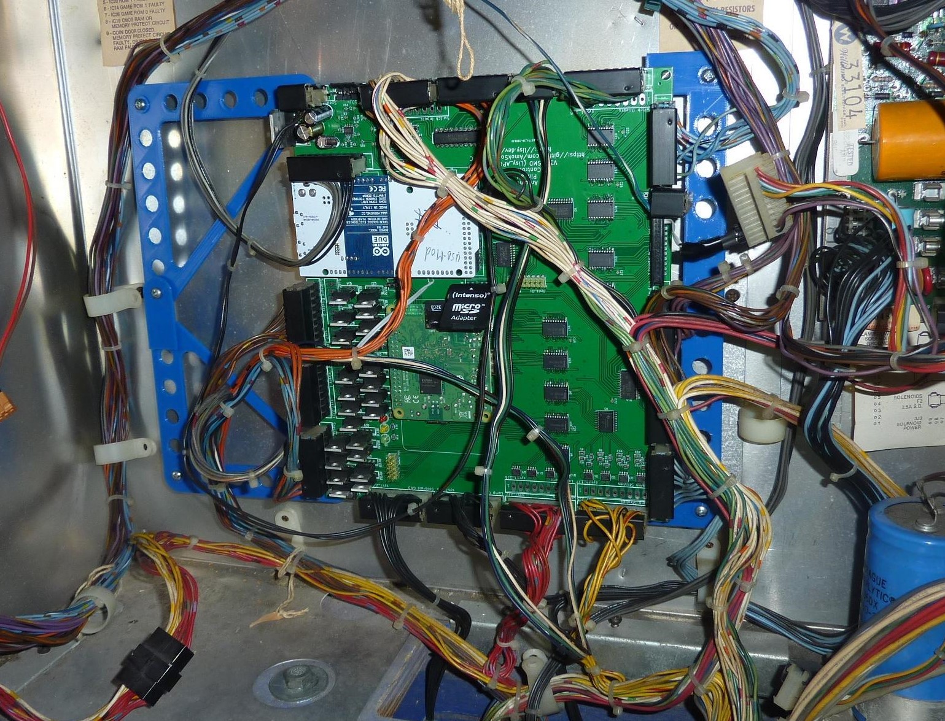
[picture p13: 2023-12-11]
DOC/PICS/FrameSys7_2.jpg

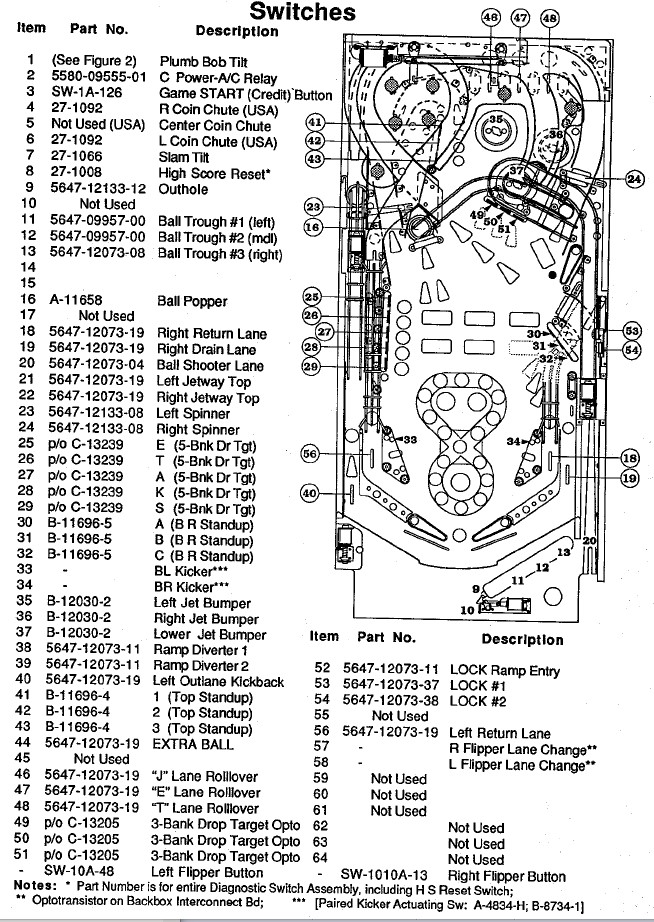
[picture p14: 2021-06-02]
DOC/PICS/RG_Sw.JPG

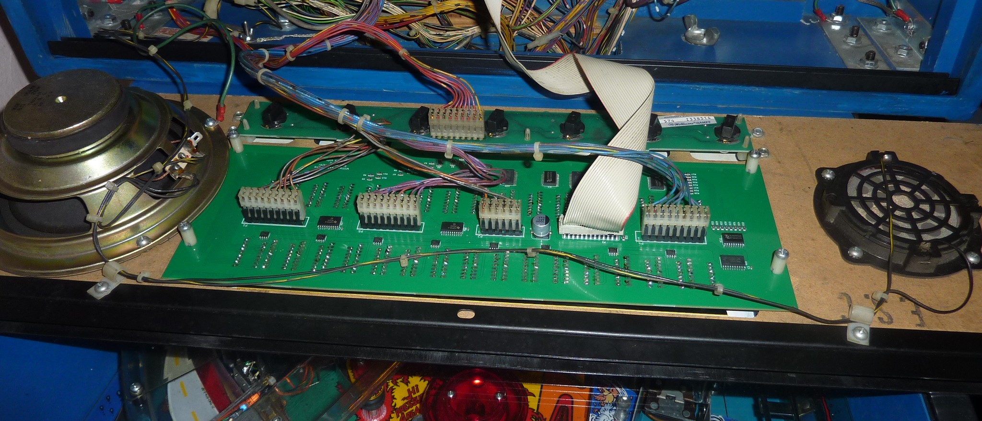
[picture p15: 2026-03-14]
DOC/PICS/Disp_Sys11b2.jpg

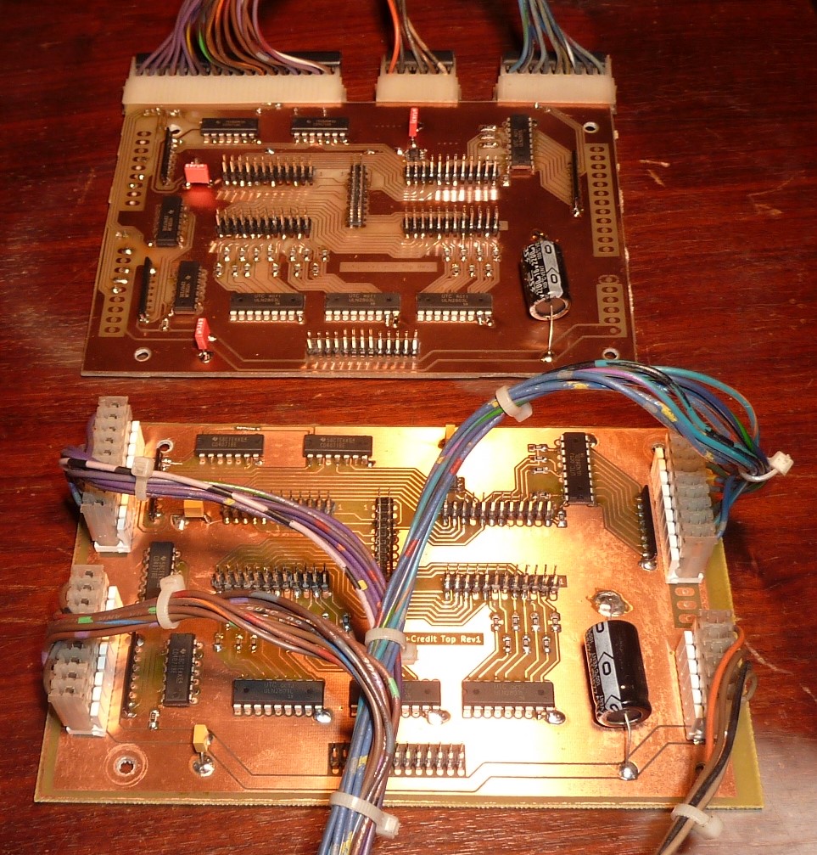
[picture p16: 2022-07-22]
DOC/PICS/Sys7_Alpha.jpg

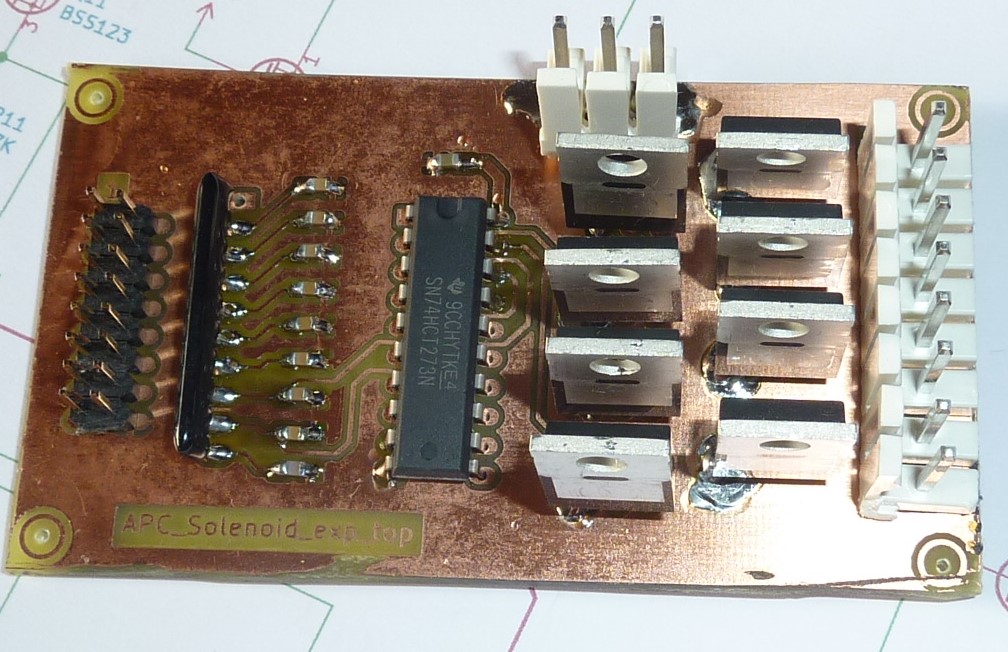
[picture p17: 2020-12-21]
DOC/PICS/SolExpBoard.JPG

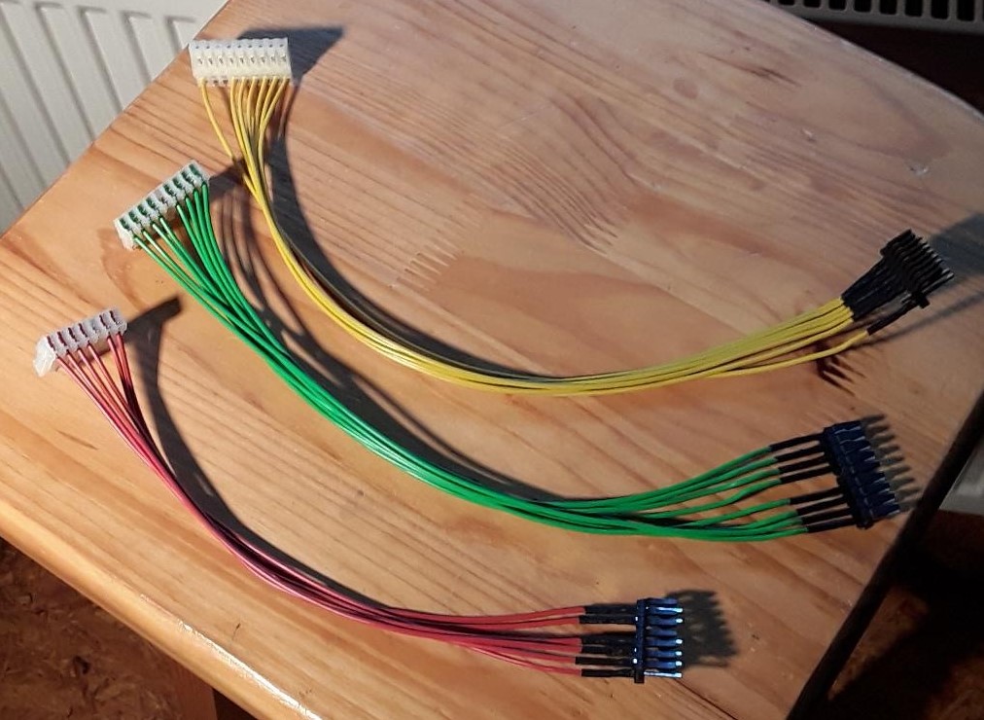
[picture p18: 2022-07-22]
DOC/PICS/Sys11cKabel.jpg

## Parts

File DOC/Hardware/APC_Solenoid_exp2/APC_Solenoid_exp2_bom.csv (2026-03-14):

Reference | Qty | Value | Footprint
C1 | 1 | 100n | Capacitor_SMD:C_0805_2012Metric_Pad1.18x1.45mm_HandSolder
C2 | 1 | 150p | Capacitor_SMD:C_0805_2012Metric_Pad1.18x1.45mm_HandSolder
J1 | 1 | APC_HW_ext | MeineLibs:pin_array_8x2_big_pads
J2 | 1 | Sol_GND | MeineLibs:Molex3
J3 | 1 | Solenoids | MeineLibs:Molex8
Q1,Q3,Q5,Q7,Q9,Q10,Q11,Q14,Q15 | 9 | BC856 | Package_TO_SOT_SMD:SOT-23
Q2,Q4,Q6,Q8,Q12,Q13,Q16,Q17 | 8 | IRL540 | MeineLibs:TO220_GDS_BP
R1 | 1 | 47K | Resistor_SMD:R_1206_3216Metric_Pad1.30x1.75mm_HandSolder
R2,R3,R5,R7,R9,R11,R12,R15,R16 | 9 | 10K | Resistor_SMD:R_1206_3216Metric_Pad1.30x1.75mm_HandSolder
R4,R6,R8,R10,R13,R14,R17,R18 | 8 | 4.7K | Resistor_SMD:R_1206_3216Metric_Pad1.30x1.75mm_HandSolder
RN1 | 1 | 4.7K | MeineLibs:SIP10_BigPads
U1 | 1 | 74HCT273 | Package_DIP:CERDIP-20_W7.62mm_SideBrazed_LongPads
U2 | 1 | ULN2803A | Package_DIP:CERDIP-18_W7.62mm_SideBrazed_LongPads

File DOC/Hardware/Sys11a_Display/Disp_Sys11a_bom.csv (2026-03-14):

Reference | Qty | Value | DNP | Exclude from BOM | Exclude from Board | Footprint | Datasheet
+5V?,+5V?,+5V?,GND?,GND?,GND?,GND?,GND?,GND?,U?,U?,U?,U?,U?,U?,U?,U?,U?,U?,U?,U?,U? | 22 | ~
AN1,AN2,AN3,AN4,AN5,AN6,AN7,AN8,AN9,AN10,AN11,AN12,AN13,AN14 | 14 | PSA08-11
C1,C2 | 2 | ELC-45
IC1A?,IC1C?,IC1D?,IC2A?,IC2B?,IC2C?,IC2D?,IC3A?,IC3C?,IC3D?,IC6A?,IC6B?,IC6C?,IC6D? | 14 | 4071
IC1P?,IC2P?,IC3P?,IC6P? | 4 | VSS |  |  |  | VDD
IC4A?,IC4B?,IC4C?,IC4D?,IC4E?,IC4F?,IC4G?,IC4H?,IC5C?,IC5D?,IC5E?,IC5F?,IC5G?,IC8A?,IC8B?,IC8C?,IC8D? | 17 | ULN2803
IC7 | 1 | ULN2803A
IRF7316 | 1 | U$1G$1,U$1G$2,U$2G$1,U$2G$2,U$3G$1,U$3G$2,U$4G$1,U$4G$2,U$5G$1,U$5G$2,U$6G$1,U$6G$2,U$7G$1
J1 | 1 | Segments2
J2 | 1 | D156C6
J3 | 1 | Strobes1
J4 | 1 | Strobes2
J5 | 1 | Segments1
N1,N2,N3,N4,N5,N6,N7,N8,N9,N10,N11,N12,N13,N14 | 14 | SA08-11
Q7 | 1 | IRF7316 |  |  |  | SO8
RN1,RN2,RN3,U$34,U$36,U$37,U$38,U$39,U$40,U$41,U$87,U$88,U$89,U$90,U$91,U$92,U$93,U$94 | 18 | 4k7
U$8,U$17,U$26,U$27,U$28,U$29,U$30,U$31,U$32,U$33,U$51,U$52,U$53,U$54,U$55,U$56,U$57,U$58,U$66,U$67,U$68,U$69,U$70,U$71,U$72 | 25 | 20R

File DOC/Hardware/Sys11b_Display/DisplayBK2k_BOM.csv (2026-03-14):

Comment | Designator | Footprint | LCSC
1000u | C1 | Capacitor_SMD:CP_Elec_10x10.5 | C336713
100n | C2,C3,C4,C5,C6,C7 | Capacitor_SMD:C_0603_1608Metric | C14663
ULN2803A | IC4,IC5,IC7,IC11 | Package_SO:SOIC-18W_7.5x11.6mm_P1.27mm | C845537
IRF7316 | Q1,Q2,Q3,Q4,Q5,Q6,Q7,Q8 | MeineLibs:SO8E | C55887
47 | R1,R2,R3,R4,R5,R6,R7,R8,R9,R10,R11,R12,R13,R14,R15,R16,R17,R18,R19,R20,R21,R22,R23,R24,R25,R26,R27,R28,R29,R30,R31,R32 | Resistor_SMD:R_1206_3216Metric | C102353
18K | R33 | Resistor_SMD:R_1206_3216Metric | C17921
74HC244 | U17,U22 | Package_SO:SOIC-20W_7.5x12.8mm_P1.27mm | C85068
74HC240 | U18,U19,U20,U21 | Package_SO:SOIC-20W_7.5x12.8mm_P1.27mm | C8094

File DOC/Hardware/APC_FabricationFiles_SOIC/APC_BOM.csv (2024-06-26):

Comment | Designator | Footprint | JLCPCB Part #（optional）
2.2u | C1,C6 | Capacitors_SMD:C_0603 | C23630
22u | C14 | Capacitors_SMD:C_0805 | C782176
100n | C25,C4,C28,C15,C22,C26,C23,C27,C19,C12,C10,C20,C29 | Capacitors_SMD:C_0603 | C14663
680p | C3,C7 | Capacitors_SMD:C_0603 | C1630
68n | C31,C30,C24,C21,C18,C17,C16,C13 | Capacitors_SMD:C_0603 | C31658
470n | C33,C32 | Capacitors_SMD:C_0603 | C1623
150p | C5,C8 | Capacitors_SMD:C_0603 | C1594
IRF7316 | Q1,Q2,Q3,Q4 | MeineLibs:SO8E | C55887
MMBT3904 | Q5,Q7 | TO_SOT_Packages_SMD:SOT-23 | C20526
S9015 | Q8 | TO_SOT_Packages_SMD:SOT-23 | C2149
IRF7341 | Q9,Q10,Q11,Q12 | MeineLibs:SO8E | C21791
10K | R21,R20,R22 | Resistors_SMD:R_1206 | C17902
10K | R68 | Resistors_SMD:R_0603 | C25804
27K | R69,R67,R65,R90,R87,R74 | Resistors_SMD:R_0603 | C22967
300K | R70,R76 | Resistors_SMD:R_0603 | C23024
15K | R71,R66 | Resistors_SMD:R_0603 | C22809
1K | R73,R2,R6,R10,R14,R4,R8,R12,R16 | Resistors_SMD:R_1206 | C4410
4.7K | R86 R72 R17 R19 R18 R1 R5 R9 R13 R3 R7 R11 R15 R77 R82 R78 R83 R79 R84 R81 R85 | Resistors_SMD:R_1206 | C17936
47K | R88 | Resistors_SMD:R_0603 | C25819
4.7K | R89 | Resistors_SMD:R_0603 | C23162
74HCT573 | U1,U2,U4 | Housings_SOIC:SOIC-20_7.5x12.8mm_Pitch1.27mm | C5209384
74HC154 | U14 | MeineLibs:SOIC-24_7.5x15.4mm_Pitch1.27mm | C13758
IRL540 | Q13 Q19 Q25 Q31 Q14 Q20 Q26 Q32 Q15 Q21 Q27 Q33 Q16 Q22 Q28 Q34 Q17 Q23 Q29 Q35 Q18 Q30 Q24 Q36 | MeineLibs:TO220_GDS_BP | C111607
LM358 | U20 | MeineLibs:SO8E | C7950
ULN2803A | U3 | Housings_SOIC:SOIC-18_7.5x11.6mm_Pitch1.27mm | C845537
74HCT273 | U5,U6,U16,U17,U18,U8,U11,U12,U15,U23 | Package_SO:SOIC-20W_7.5x12.8mm_P1.27mm | C2652822
SD_adapter | P14 | MeineLibs:uSD_TF-01 | C91145
2x40 pin header | J1 | 2,54mm | C2834348
CH3.96-9A | 1J6,1J7,2J12,2J13,sys11_1J10,sys11_1J11,sys11_1J12,sys11_1J6,sys11_1J7,sys11_1J8,sys7_1J2,sys7_2J10,sys7_2J11,sys7_2J2,sys7_2J3,sys7_2J4,sys7_2J5,sys7_2J6,sys7_2J7,sys7_2J9 | CONN-TH_CH3.96-9A | C10586
CH3.96-4A | 10J2,10J4,1J4 | CONN-TH_CH3.96-4A | C10379
CH3.96-12A | 1J5 | CONN-TH_CH3.96-12A | C10589
B-2100S36P-B110 | P4 | CONN_36_2x18 | C168945
B-2100S12P-B110 | P12 | Lisy_Jumper_2x6 | C124388
MTP125-1213S1 | 1J8 | Display Segments 2_2x13 | C358701
C68234 | P11 | Sys11_J21_2x8 | C68234
B-2200S06P-B120 | P7 | CONN_3X2(Female) | C124421
B-2200S06P-A120 | P8 | SD_card_1x6(Female) | C124415
B-2100S04P-A110 | P9 | Ardu_pwr_1x4 | C124378
PZ254V-11-02P | P6,P13 | CONN_2,1x2 | C492401
A2541WV-6P | P1 | CONN_6,1x6 | C225481
X6511WV-07H-C30D60 | P2 | CONN_7,1x7 | C706879
Z-211-0811-0021-001 | P5 | CONN_8,1x8 | C190820
Tacticle Switch | SW1 | KEY-TH_4P | C273473
A09-472JP | RR1,RR7 | Array SIP-9 4.7K | C9112
1000uF 16V | C9 | Radial,10X16mm | C88751
100uF 25V | C2 | Radial,6.3X11mm | C106598
470uF 35V | C11 | Radial,10X12.5mm | C127917
LED red | D1 | 3mm | C2286
LED yellow | D2 | 3mm | C72038
LED green | D3 | 3mm | C72043

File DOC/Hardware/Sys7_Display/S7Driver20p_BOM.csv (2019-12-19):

Reference | Value | Footprint | Datasheet
C5 | 100n | 1 | 2
C6 | 100n | 1 | 2
C7 | 100n | 1 | 2
CREDIT1 | PINHD-2X10
IC5 | 4050
IC8 | 4081
PLAYER1 | PINHD-2X10
PLAYER2 | PINHD-2X10
PLAYER3 | PINHD-2X10
PLAYER4 | PINHD-2X10
POWER1 | PADROW6
Q5 | IRF7316
U$2 | 20
U$24 | 6.8K
IC3 | 4511
IC4 | 4511
STROBE1 | PADROW18
BCD-IN1 | PADROW9
Q1 | IRF7316
IC7 | 4050
Q8 | IRF7316
Q6 | IRF7316
Q7 | IRF7316
IC6 | 4050
Q2 | IRF7316
Q3 | IRF7316
Q4 | IRF7316
U$3 | 20
U$4 | 20
U$5 | 20
U$6 | 20
U$7 | 20
U$8 | 20
U$27 | 20
U$28 | 20
U$29 | 20
U$30 | 20
U$31 | 20
U$32 | 20
U$33 | 20
U$26 | 20
U$34 | 20
U$25 | 20
U$1 | 20
IC1 | ULN2803A
IC2 | ULN2803A
C3 | 100n | 1 | 2
C2 | 100n | 1 | 2
C4 | 100n | 1 | 2
C1 | 4700u |  | ~

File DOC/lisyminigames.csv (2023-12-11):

No | Mame Name | Long Name | Type | throttle | comment
0 | httip_l1 | Hot Tip | SYS3 | 120
1 | lucky_l1 | Lucky Seven | SYS3 | 120
2 | wldcp_l1 | World Cup | SYS3 | 120
3 | cntct_l1 | Contact | SYS3 | 120
4 | disco_l1 | Disco Fever | SYS3 | 120
5 | phnix_l1 | Phoenix | SYS4 | 120
6 | flash_l1 | Flash | SYS4 | 120
7 | flash_l2 | Flash | SYS4 | 120
8 | trizn_l1 | Tri Zone | SYS4 | 120
9 | pkrno_l1 | Pokerino | SYS4 | 120
10 | tmwrp_l2 | Time Warp | SYS4 | 120
11 | stlwr_l2 | Stellar Wars | SYS4 | 120
12 | lzbal_l2 | Laser Ball | SYS6 | 120
13 | scrpn_l1 | Scorpion | SYS6 | 120
14 | blkou_l1 | Blackout | SYS6 | 120
15 | grgar_l1 | Gorgar | SYS6 | 120
16 | frpwr_l6 | Firepower | SYS6 | 120
17 | algar_l1 | Algar | SYS6A | 120
18 | alpok_l6.zip | Alien Poker | SYS6A | 120
19 | csmic_l1 | Cosmic Gunfight | SYS7 | 120
20 | jngld_l2 | Jungle Lord | SYS7 | 120
21 | pharo_l2 | Pharaoh | SYS7 | 120
22 | solar_l2 | Solar Fire | SYS7 | 120
23 | prototy | Thunderball | SYS7 | 120
24 | hypbl_l6 | Hyperball | SYS7 | 120
25 | barra_l1 | Barracora | SYS7 | 120
26 | vrkon_l1 | Varkon | SYS7 | 120
27 | wrlok_l3 | Warlok | SYS7 | 120
28 | dfndr_l4 | Defender | SYS7 | 120
29 | jst_l2 | Joust | SYS7 | 120
30 | lsrcu_l2 | Laser Cue | SYS7 | 120
31 | fpwr2_l2 | Firepower II | SYS7 | 120
32 | ratrc_l1 | Rat Race | SYS7 | 120
33 | strlt_l1 | Star Light | SYS7 | 120
34 | bk_l4 | Black Knight | SYS7 | 120
35 | tmfnt_l5 | Time Fantasy | SYS7 | 120
36 | pfevr_l2 | Pennant Fever | SYS8 | 120
37 | sshtl_l7.zip | Space Shuttle | SYS9 | 120
38 | sorcr_l2 | Sorcerer | SYS9 | 120
39 | comet_l5 | Comet | SYS9 | 120
40 | hs_l4 | High Speed | SYS11 | 120
41 | grand_l4 | Grand Lizard | SYS11 | 120
42 | rdkng_l4 | Road Kings | SYS11RK | 120
43 | pb_l5 | Pinbot | SYS11A_ | 120
44 | f14_l1 | F-14 Tomcat | SYS11A_ | 120
45 | fire_l3 | Fire! | SYS11A | 120
46 | milln_l3 | Millionaire | SYS11A | 120
47 | bguns_l8 | Big Guns | SYS11B | 120
48 | spstn_l5 | Space Station | SYS11B | 120
49 | gmine_l2 | Gold Mine | SYS11B | 120
50 | cycln_l5 | Cyclone | SYS11B | 120
51 | bnzai_l3 | Banzai Run | SYS11B | 120
52 | swrds_l2 | Swords of Fury | SYS11B | 120
53 | taxi_l4 | Taxi | SYS11B | 120
54 | tdawg_l1 | Top Dawg | SYS11B | 120
55 | jokrz_l6 | Jokerz! | SYS11B | 120
56 | esha_la3 | Earthshaker | SYS11B | 120
57 | bk2k_l4 | Black Knight 2000 | SYS11B | 120
58 | tsptr_l3 | Transporter the Rescue | SYS11B | 120
59 | polic_l4 | Police Force | SYS11B | 120
60 | shfin_l1 | Shuffle Inn | SYS11B | 120
61 | afm_11b | Elvira and the Party Monsters | SYS11B | 120
62 | bcats_l5 | Bad Cats | SYS11B | 120
63 | mousn_l1 | Mousin' Around! | SYS11B | 120
64 | whirl_l3 | Whirlwind | SYS11B | 120
65 | gs_l4 | The Bally Game Show | SYS11C | 120
66 | pool_l7 | Pool Sharks | SYS11C | 120
67 | rollr_l3 | Rollergames | SYS11C | 120
68 | diner_l4 | Diner | SYS11C | 120
69 | radcl_l1 | Radical! | SYS11C | 120
70 | dd_l2 | Dr. Dude | SYS11C | 120
71 | rvrbt_l3 | Riverboat Gambler | SYS11RG | 120
72 | bbnny_l2 | Bugs Bunny's Birthday Ball | SYS11C | 120
73 | lwar_a83 | Laser War | DE_A1 | 120
74 | ssvc_a26 | Secret Service | DE_A2 | 120
75 | torp_e21 | Torpedo Alley | DE_A2 | 120
76 | tmac_a24 | Time Machine | DE_A2 | 120
77 | play_a24 | Playboy 35th Anniversary | DE_A2 | 120
78 | mnfb_c27 | Monday Night Football | DE_A2 | 120
79 | robo_a34 | Robocop | DE_A2 | 120
80 | poto_a32 | Phantom of the Opera | DE_A2 | 120
81 | bttf_a28 | Back to the Future | DE_A2 | 120
82 | simp_a27 | The Simpsons | DE_A3 | 120

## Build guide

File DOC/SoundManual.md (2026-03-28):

# Manual sound file generation

## Which sounds are required?

System 11 boards can handle 8 bit sound commands which leads to a possible number of 256 sounds per board minus some control commands, but only a part of these numbers are actually used by a game.  
Most System11 machines have audio circuits on the CPU board (referred to as board 0) and a seperate audio board (board 1). With System11c Williams stopped populating the audio circuits on the CPU board, so these games only have the audio board 1.

System 9 boards can handle 8 bit sound commands which leads to a possible number of 256 sounds minus some control commands, but only a part of these numbers are actually used by a game. They have only one audio board, so the board prefix is always 0.

With this manual method we have to extract and preprocess every sound by hand, so we try to keep the number of sounds as low as possible by just extracting those which are actually requested by PinMame.

When you start from scratch you should play your game with Lisy being in Sound Debug Mode. Please read the [Controlling Lisy page](https://github.com/AmokSolderer/APC/blob/master/DOC/LisyDebug.md) to learn how to do this.

Now start a game and let Lisy log the sound commands. This will already give you the most common sound numbers to start with. Later you'll have to repeat this step or use the [Audio Debug Mode](https://github.com/AmokSolderer/APC/blob/master/DOC/PinMameSound_9.md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) of the APC to find the remaining missing sounds.

When you're done press the shutdown switch SW1 on your APC board to make it exit the emulation and store the log file on the SD card. The file will be located on the Pi's SD card in the folder lisy/lisy_m/debug.

In lisy_m_debug.txt playing a sound looks like

    [461.372965][0.000064] LISY_W sound_handler: board:0 0x79 (121)
    [461.372985][0.000020] play soundindex 121 on board 0 
    [461.373005][0.000020] USB_write(3 bytes): 0x32 0x01 0x79

In this case sound 0x79 shall be played on board 0 which means you have to record the sound command 0079 in PinMame. If it was board 1 then the sound command would be 0179.

The Lisy sound debug log only tells you which sound numbers are needed for your game. Now it's time to extract the corresponding sound files.

## Manual extraction from PinMame

In PinMame, press F4 to enter the 'Sound Command Mode' then press DEL for the Manual / Command Mode.

The following steps have to be repeated for every sound you want to record. That means you have to do it for every sound number you've found in the Lisy sound debug log.  
Enter the prefix and the hexadecimal sound number you have derived from the Lisy log. Then press F5 to start the recording, SPACE to play the sound and F5 again to stop recording when the sound has played out. The sound can be found in PinMame's 'wave' folder.  
The sound command 00 (with the corresponding prefix) stops the currently playing sound / music.  
Not all sound numbers play a sound in PinMame, as some are just controlling the audio board. These commands have to be covered by PinMameExceptions and can be ignored for now.

## Use the correct file names

Remember to rename the files immediately to the correct names to avoid confusion. The APC needs the names in the format [single digit board prefix]_[sound number in hex].wav, so the name for the 0079 sound would be 0_79.wav

## Preprocessing the WAV files with Audacity

For some reason the Windows version of PinMame generates sounds having a sampling rate of 48KHz. These must be converted to the normal sampling rate of 44.1KHz. Sound files generated by Unix PinMame already have the correct sampling rate.  
Furthermore, the volume of the sound and music files generated by PinMame differs quite a lot. You can use a free audio editor like Audacity (https://www.audacityteam.org) to do all necessary adjustments.

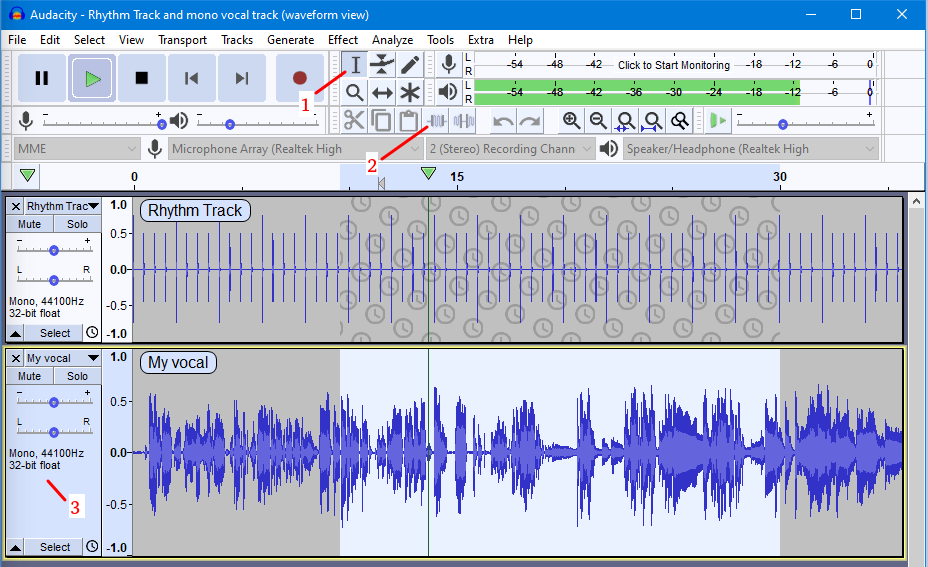
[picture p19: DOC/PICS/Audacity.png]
Audacity


This is the manual way to preprocess a file recorded from PinMame.

* Open the file with Audacity
* Press the button for the Selection Tool (1) and select the part of the sound you want to use
* Delete the rest (2)
* Click inside the cyan box next to the waveform (3) to select the whole track
* Select the 'Tracks -> Sampling rate' menu and set the sampling rate to 44100Hz (skip this for Unix PinMame)
* If you have a stereo track, use the 'Tracks -> Mix -> Mix Stereo Down to Mono' menu to get mono (not needed for PinMame generated files)
* Select the 'Effect -> Normalize' menu to open the window with the normalizing options
* Select 'Remove DC offset' and 'Normalize peak amplitude to' the volume of your choice.
* Select the 'File -> Export -> Export Selected Audio...' and save it with the 'Signed 16-bit PCM' encoding

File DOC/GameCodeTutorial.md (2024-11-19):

# How to create my own game code?

Let‘s assume you just built your own APC board and put it in your pinball machine. You have probably tested the adapted BaseCode.ino as described in [Setting up the BaseCode](https://github.com/AmokSolderer/APC/blob/master/DOC/SetUpBC.md) and now you‘re keen to write your own stuff. In this document I will generate a tutorial code sheet as an example to explain how to do so. In my case the tutorial is supposed to run in a Rollergames pinball, but you can adapt it to other machines or just read it to understand the principles of the APC API. Please use the [APC software reference](https://github.com/AmokSolderer/APC/blob/master/DOC/Software/APC_SW_reference.pdf) to get an overview about the available commands and variables.

## 1 Adding a new codesheet
First of all I copy my modified BaseCode.ino and rename it to a new .ino file in the APC folder. In my case I create the file Tutorial.ino in the APC folder where APC.ino, BlackKnight.ino and so on are already present. Then I change all BC_ prefixes to those of my own game to avoid compilation errors. For the Tutorial, I change them all to TT_.
### 1.1 The GameDefinition structure
After changing all the prefixes, my GameDefinition structure looks like this:

    struct GameDef TT_GameDefinition = {
        TT_setList,                           // GameSettingsList
        (byte*)TT_defaults,                   // GameDefaultsPointer
        "TT_SET.BIN",                         // GameSettingsFileName
        "TT_SCORE.BIN",                       // HighScoresFileName
        TT_AttractMode,                       // AttractMode
        TT_SolTimes};                         // Default activation times of solenoids

Every game has its own highscore and settings file to be stored on the SD card. The two filenames  tell the system which names to use. They can be chosen freely as long as they don‘t exceed 8 characters. The other variables have to be defined as follows.
### 1.2 Changing the settings menu
TT_setList has to be a list of SettingTopic structures. They determine how the game settings menu of my Tutorial machine will look like and how these settings will be handled. As an example there is a 'God Mode' defined in the Base Code settings (whatever this might be, but it can't harm to have one). I leave it as it is, which makes my settings list look like this:

    struct SettingTopic TT_setList[5] = {{"  GOD   MODE  ",HandleBoolSetting,0,0,0}, // defines the game specific settings
      {" RESET  HIGH  ",TT_ResetHighScores,0,0,0},
      {"RESTOREDEFAULT",RestoreDefaults,0,0,0},
      {"  EXIT SETTNGS",ExitSettings,0,0,0},
      {"",NULL,0,0,0}};

As you can only turn this mode on or off, we define it as a boolean setting (for more details on settings refer to the SelSetting command in the APC_Software_Reference). 
The „Restore Defaults“ and „Exit Settings“ topics are probably self explaining and the last one filled with zeros is necessary to indicate the end of the list.  
Now that we have defined the game settings menu we also need the corresponding setting values. The APC software uses an array of 64 byte to store those values:

    byte game_settings[64];   // game settings to be stored on the SD

When a SD card is detected during startup and a file with the name specified above is found (TT_SET.BIN) then its content is read into the game_setting array. If a file could not be found the pointer on position 2 of the game definition (TT_defaults) is used to read the default values. These values are also used if you choose Restore Default in the game settings menu.  
As I want to have to non-god mode as default, I can leaves the array as it is: 

    const byte TT_defaults[64] = {0,0,0,0,0,0,0,0,    // game default settings
              0,0,0,0,0,0,0,0,
              0,0,0,0,0,0,0,0,
              0,0,0,0,0,0,0,0,
              0,0,0,0,0,0,0,0,
              0,0,0,0,0,0,0,0,
              0,0,0,0,0,0,0,0,
              0,0,0,0,0,0,0,0};

The default values have to be in the same order as the elements in TT_setList.  
If you want to know more about the settings system, please refer to the APC_setList in APC.ino, since the SettingTopic structure is also used for the system settings. That means you can find all the stuff mentioned above again in the APC.ino file with some real content and APC_ as the prefix. 
The next topic of my game definition tells the system how to enter the game code. Since a normal game starts with the attract mode, the corresponding pointer is named TT_AttractMode. For starters I just uncomment the TT_AttractMode copied from the Base Code and change it to this:  

    void TT_AttractMode() {
      DispRow1 = DisplayUpper;
      DispRow2 = DisplayLower;
      WriteUpper("MY NEW GAME     ");}

The last topic of my new game definition is the TT_SolTimes. This is quite important as it tells the system what is the default turn on time for each solenoid in milliseconds.  
To understand the importance of this just remember that we have different kinds of solenoids in a pinball machine and that motors, magnets and flashers are also handled by the solenoid drivers. Strictly spoken this solenoid times should be set before you even activate your solenoids for the first time because otherwise you won‘t be able to test them properly. However for the beginning you can fill all values with 30 which is not enough to really activate a motor or a magnet but at least you won‘t have any burnt coils because of the turn on times being too long.  
For my Rollergames I choose 100ms for all flashers, 999ms for motors and relays. For solenoids 30ms is a good value to start and if you want more power try it with 50ms.
### 1.3 Adding a new game
Now that we have completed the game definition, we have to make the system use it. There is a subroutine named TT_init for this where TT_GameDefinition is selected.

    void TT_init() {
      ACselectRelay =  TT_ACselectRelay;  // assign the number of the A/C select relay
      GameDefinition = TT_GameDefinition;}  // read the game specific settings and highscores

Finally the new game code must be implemented into the APC.ino program. For this you have to locate the „Active Game“ menu entry in the APC_setList. 

    {" ACTIVE GAME ",HandleTextSetting,&TxTGameSelect[0][0],0,4},

The handler indicates a text setting with the different text entries being in TXTGameSelect. Increase the last number by one, as this is the number of available settings and we're about to add one. The 4 from above means that I have 5 game entries (the system starts counting with 0). After that I change TXTGameSelect to

    char TxTGameSelect[5][17] = {{" BASE  CODE     "},{" BLACK KNIGHT   "},{"    PINBOT      "},{"  USB  CONTROL  "},{"  TUTORIAL      "}};

which means that from now on Tutorial will be listed in my „Active Game“ selection  menu and the variable APC_setting[ActiveGame] will become 4 when it is selected.  

The last step is to locate Init_System2 in APC.ino where the initialization routine of the selected game is called after the system has started. With my tutorial included the switch statement of my selected game looks like this:

    void Init_System2(byte State) {
      switch(APC_settings[ActiveGame]) {  // init calls for all valid games
      case 0:
        BC_init();
        break;
      case 1:
        BK_init();
        break;
      case 2:
        PB_init();
        break;
      case 3:
        USB_init();
        break;
      case 4:
        TT_init();
        break;
      default:
        WriteUpper("NO GAMESELECTD  ");
        while (true) {}
      }

If you start this, your pinball will first complain about missing files for highscores and game settings. After that it should show „MY FIRST GAME“ in the displays and that was it. Now it's time  to add some functionality.

## 2 Basic game functions

Until now we just have shown some text in the displays, so it's time to add some functionality.

### 2.1 Lamps

In order to use lamps we have to set the LampPattern pointer to an array which stores the state of all lamps. The array consists of lamp columns with each one storing the state of 8 lamps. That means we need 8 columns to store the state of all 64 lamps. If you don't want to do something fancy, you don't have to care about this, just be sure to add

    LampPattern = LampColumns;    // point to the standard lamp array

to your code. This will make your system use the standard lamp array which is used by all lamp related commands.

Turning on a lamp is quite simple. Just get the number of the lamp you want to turn on from your pinball's manual and use

    TurnOnLamp(LampNumber);

to do so. The corresponding command to turn it off is

    TurnOffLamp(LampNumber);

If you want to make a lamp blink use

    AddBlinkLamp(LampNumber, Period in ms);

To stop the blinking use

    RemoveBlinkLamp(LampNumber);

Note that all lamps having the same blinking period are blinking synchronously.

With all the above added, our programm should look like this:

    void TT_AttractMode() {                         // Attract Mode
      DispRow1 = DisplayUpper;
      DispRow2 = DisplayLower;
      WriteUpper("MY NEW GAME     ");
      LampPattern = LampColumns;                    // point to the standard lamp array
      TurnOnLamp(53);
      AddBlinkLamp(54, 250);}

In this example lamp 53 is turned on permanently while lamp 54 is blinking with a period of 250ms (4 times per second)

### 2.2 Switches

The APC offers two ways to use switches. First you can use

    QuerySwitch(SwitchNumber);

to get the current status of a switch. A return value of 'true' means that the switch is activated.

The second way is to use a switch handler, which is a program that is called when a switch is activated or released. For now we want to handle only switches being activated.

    Switch_Pressed = TT_TestSW;
    Switch_Released = DummyProcess;

If a switch is activated (pressed) the routine TT_TestSW will be called with the switch number as the argument. As we don't want to handle released switches, we just set the Switch_Released pointer to the DummyProcess, which does exactly nothing.

### 2.3 Solenoids

First, let's bring the drop target bank of my Rollergames to live. For this, my first switch handler looks like this:

    void TT_TutorialSW(byte SwitchNo) {
      switch (SwitchNo) {
      case 8:                                       // high score reset
        digitalWrite(Blanking, LOW);                // invoke the blanking
        break;
      case 49:
      case 50:
      case 51:
        if (QuerySwitch(49)) {
          TurnOnLamp(49);}
        if (QuerySwitch(50)) {
          TurnOnLamp(50);}
        if (QuerySwitch(51)) {
          TurnOnLamp(51);}
        if (QuerySwitch(49) && QuerySwitch(50) && QuerySwitch(51)) {
          ActA_BankSol(6);
          TurnOffLamp(49);
          TurnOffLamp(50);
          TurnOffLamp(51);}}}

Whenever a switch is activated the above handler will be called with the number as an argument. An easy way to handle the various switch is just to use a switch statement.

Don't be confused by switch number 8 as it's just to spare your lamps and displays. If you upload new software into the Arduino on the APC, it can happen that the lamps and displays are getting brighter than normal for a very short time. This wont damage them, but they're not going to like it either. To prevent this from happening just press the _High Score Reset_ button before the upload. This will invoke the blanking which causes lamps, displays and coils to be switched off.

The important part is the handling of the switches 49, 50 and 51. In the Rollergames these switches belong to the drop targets and the numbers are even matching to the corresponding lamps. In my case I'm just checking for every drop target switch whether it is active and in case that it is, the corresponding lamp is lit. If all targets are down, all lamps are turned off and the reset coil of the target bank is activated.

If your machine also has drop targets you can just change the lamp, Switch and coil numbers and try it yourself. But be careful with your fingers when dropping the targets as they're coming up immediately when all three are down.

### 2.3 Timers

Now, let's assume we want to have timed drop targets. Most machines with timed targets have a blinking lamp nearby to indicate a certain urgency. The Rollergames has none, but I just assign this task to lamp 53. This changes my switch handler to

    void TT_TutorialSW(byte SwitchNo) {
      static byte DropTimer = 0;
      switch (SwitchNo) {
      case 8:                                          // high score reset
        digitalWrite(Blanking, LOW);                   // invoke the blanking
        break;
      case 49:                                         // drop targets
      case 50:
      case 51:
        if (QuerySwitch(49) && QuerySwitch(50) && QuerySwitch(51)) {  // all targets down?
          if (DropTimer) {// timer running?
            KillTimer(DropTimer);                      // stop timer
            DropTimer = 0;                             // and indicate it
            RemoveBlinkLamp(53);}                      // turn off blinking lamp
          ActA_BankSol(6);}                            // reset drop targets
        else {                                         // not all targets down
          if (!DropTimer) {                            // timer not yet running?
            AddBlinkLamp(53, 500);                     // start blinking lamp
            DropTimer = ActivateTimer(5000, 100, TT_TutorialSW);}}  // start timer for 5s
        break;
      case 100:                                        // timer has run out
        DropTimer = 0;                                 // indicate it
        RemoveBlinkLamp(53);                           // turn off blinking lamp
        ActA_BankSol(6);                               // reset drop targets
        break;}}

In this example I'm using a timer to reset the drop targets 5 seconds after the first target has been hit. 

    DropTimer = ActivateTimer(5000, 100, TT_TutorialSW);}}  // start timer for 5s

In this line a timer is activated with a running time of 5000ms. After this time it will call TT_TutorialSW with an argument value of 100. When this call happens the DropTimer variable is set to 0 to indicate that no timer is running which also means that all drop targets are up. Afterwards the blinking lamp 53 is turned off and the drop target bank is reset.

If all three targets have been knocked down by the player the targets have to be re-set immediately and the timer must be deactivated. In order to deactivate a timer you need it's number which is returned by the ActivateTimer command when the timer is being started. Here, this number is being stored in the DropTimer variable and the KillTimer(DropTimer) command is used to get rid of the timer.

Why to call TT_TutorialSW and not some additional routine? 

Both will work, but with an additional routine you would need a global variable to store the timer number and an additional routine. Both is not necessarily harmful, but I prefer to keep to number of global variables and routines low to make the code easier to read and to indicate what belongs together.

Of course if there's no need to kill a timer you don't have to store it's number. As an example let's try to avoid the drop targets being re-set immediately when the last target comes down. In a game this would probably knock the ball up against the glass or hamper the target reset because the ball is still above them. Instead I would like to wait for 200ms before resetting the targets. In the code you would move the corresponding ActA_BankSol(6) command to a new routine with the name TT_ResetDropTargets(byte Dummy) and just call it by 

    ActivateTimer(200, 0, TT_ResetDropTargets);

## 3 A real game base
Until now I have just explained how to control the basic hardware functions of the APC which basically should be all you need to start your own game code, but it's still a lot to do before the first ball is put into the plunger lane and drained balls are correctly handled. The BaseCode contains a basic framework with all the stuff necessary to run a game. So let's restore the original state of TT_AttractMode():

    void TT_AttractMode() {                             // Attract Mode
      DispRow1 = DisplayUpper;
      DispRow2 = DisplayLower;
      WriteUpper("MY NEW GAME     ");
      LampPattern = LampColumns;                        // point to the standard lamp array
      //TurnOnLamp(53);
      //AddBlinkLamp(54, 250);
      Switch_Pressed = TT_AttractModeSW;
      //Switch_Pressed = TT_TutorialSW;
      //Switch_Released = DummyProcess;}
      digitalWrite(VolumePin,HIGH);                    // set volume to zero
      LampPattern = NoLamps;
      AppByte2 = 0;
      LampReturn = TT_AttractLampCycle;
      ActivateTimer(1000, 0, TT_AttractLampCycle);
      TT_AttractDisplayCycle(0);}

The first of the new commands is muting the sound by setting the VolumePin to High state. Then all lamps are turned off by settings the LampPattern pointer to NoLamps. Next is setting the LampReturn pointer to TT_AttractLampCycle which is controlling the lamp animations by using the ShowLampPatterns command during Attract Mode and then calling this routine with a timer. 

### 3.1 ShowLampPatterns
The ShowLampPatterns command provides an easy way to show complex lamp animations for playfield lamps. Hence, it ignores the first 8 lamps as they're usually located in the backbox. To use it create an array of LampPat structures. They consist of a 16bit duration value which determines how long a pattern is shown in ms and the corresponding lamp pattern array which uses bytes to define the status for every lamp. A simple example can be found at the beginning of Tutorial.ino. TT_AttractPat1 starts with lamp 9 and proceeds to the next after 250ms. Basically this does the same as the single lamp test in the test mode, but only for lamps starting from 9.

    // Duration..11111110...22222111...33322222...43333333...44444444...55555554...66666555
    // Duration..65432109...43210987...21098765...09876543...87654321...65432109...43210987
           250,0b00000001,0b00000000,0b00000000,0b00000000,0b00000000,0b00000000,0b00000000},

The example above will light lamp 9 for 250ms before moving on to the next row. The two lines above are to help you locate the right lamps, by showing the number of the lamp below with the upper row indication the decade of the lamp number. The last row of such an array is marked by the duration being zero.  

To use ShowLampPattern, the global variable PatPointer must point to the pattern array and FlowRepeat specifies the number of repetitions to be shown. A simple program to play various sequences is shown below

    void TT_AttractLampCycle(byte Event) {            // play multiple lamp pattern series
      static byte Phase;
      if (Event == 1) {                               // initial call?
        Phase = 0;}                                   // reset cycle phase
      PatPointer = TT_AttractFlow[Phase].FlowPat;     // set the pointer to the current series
      FlowRepeat = TT_AttractFlow[Phase].Repeat;      // set the repetitions
      Phase++;                                        // increase counter
      if (!TT_AttractFlow[Phase].Repeat) {            // repetitions of next series = 0?
        Phase = 0;}                             // reset counter
      ShowLampPatterns(1);}                           // call the player

Here an additional array TT_AttractFlow ist used to store the pattern sequence to be played and the number of repetitions. By setting the LampReturn pointer to TT_AttractLampCycle it is ensured that it will be called again when ShowLampPatterns has completed the sequence. Then it has has to set the required pointers to the next sequence and run ShowLampPatterns again. In order to be able to stop the lamp animations, you can either add a stop functionality to TT_AttractLampCycle or you can call ShowLampPatterns(0) with the zero being the signal for it to stop.

### 3.2 Attract mode display cycling
Usually the basic stuff being displayed during attract mode is the name of the machine, the points of the last game (if there was any) and the highscores.

    void TT_AttractDisplayCycle(byte Step) {
      TT_CheckForLockedBalls(0);
      switch (Step) {
      case 0:
        WriteUpper2("THE APC TUTORIAL");
        ActivateTimer(50, 0, ScrollUpper);
        WriteLower2("                ");
        ActivateTimer(1000, 0, ScrollLower2);
        if (NoPlayers) {                             // if there were no games before skip the next step
          Step++;}
        else {
          Step = 2;}
        break;
      case 1:
        WriteUpper2("                ");             // erase display
        WriteLower2("                ");
        for (i=1; i<=NoPlayers; i++) {               // display the points of all active players
          ShowNumber(8*i-1, Points[i]);}
        ActivateTimer(50, 0, ScrollUpper);
        ActivateTimer(900, 0, ScrollLower2);
        Step++;
        break;
      case 2:                                        // Show highscores
        WriteUpper2("1>              ");
        WriteLower2("2>              ");
        for (i=0; i<3; i++) {
          *(DisplayUpper2+8+2*i) = DispPattern1[(HallOfFame.Initials[i]-32)*2];
          *(DisplayUpper2+8+2*i+1) = DispPattern1[(HallOfFame.Initials[i]-32)*2+1];
          *(DisplayLower2+8+2*i) = DispPattern2[(HallOfFame.Initials[3+i]-32)*2];
          *(DisplayLower2+8+2*i+1) = DispPattern2[(HallOfFame.Initials[3+i]-32)*2+1];}
        ShowNumber(15, HallOfFame.Scores[0]);
        ShowNumber(31, HallOfFame.Scores[1]);
        ActivateTimer(50, 0, ScrollUpper);
        ActivateTimer(900, 0, ScrollLower2);
        Step++;
        break;
      case 3:
        WriteUpper2("3>              ");
        WriteLower2("4>              ");
        for (i=0; i<3; i++) {
          *(DisplayUpper2+8+2*i) = DispPattern1[(HallOfFame.Initials[6+i]-32)*2];
          *(DisplayUpper2+8+2*i+1) = DispPattern1[(HallOfFame.Initials[6+i]-32)*2+1];
          *(DisplayLower2+8+2*i) = DispPattern2[(HallOfFame.Initials[9+i]-32)*2];
          *(DisplayLower2+8+2*i+1) = DispPattern2[(HallOfFame.Initials[9+i]-32)*2+1];}
        ShowNumber(15, HallOfFame.Scores[2]);
        ShowNumber(31, HallOfFame.Scores[3]);
        ActivateTimer(50, 0, ScrollUpper);
        ActivateTimer(900, 0, ScrollLower2);
        Step = 0;}
      ActivateTimer(4000, Step, TT_AttractDisplayCycle);}

In order to start the display cycling, the The PB_AttractDisplayCycle subroutine has to be called once from the attract mode. After that it can be regarded as an own and independent process which calls itself all 4s to update the displays.  
As the timer number is not stored this time, the only way to stop this process is to call KillAllTimers() which kills all timers and therefore stops all processes. Normally this is not the most elegant way of process handling, but as the attract mode has quite some processes running, it makes sense to stop everything and start from scratch when leaving it.

However, using KillAllTimers has it's pitfalls when dealing with processes keeping track of their timers by themselves. Most of these processes use static variables to store the number of the timer they're currently using. If the timer is killed without the process being notified the static variable will still hold the value of a timer which doesn't exist any more. If for some reason the process is now ordered to stop, it might try to kill it's timer. If you're lucky this will just lead to an Error 11, which means that you have tried to kill a timer which is not in use. But if the corresponding timer is now being used by another process, then it will be killed which can lead to all kinds of problems that are really hard to track. For this reason you should be aware of which process is using timers in which phase of the game and you should take an Error 11 very seriously when it occurs as it means that you have lost track of your timers. An Error 11 will freeze the game in debug mode, when the 'Debug Mode' setting is set to 'no' the error will just be shown in the displays for some seconds, but the game will continue.

### 3.3 Attract mode switch handler

Now you know how to produce some light and display animations in the attract mode, but how to leave it? For this we need a switch handler. In void TT_AttractMode() of this Tutorial we have set

    Switch_Pressed = TT_AttractModeSW;

which means that this routine is being called when a switch is activated. The corresponding target routine looks like this:

    void TT_AttractModeSW(byte Button) {            // Attract Mode switch behaviour
      switch (Button) {
      case 8:                                       // high score reset
        digitalWrite(Blanking, LOW);                // invoke the blanking
        break;
      case TT_OutholeSwitch:                        // outhole
        ActivateTimer(200, 0, TT_CheckForLockedBalls); // check again in 200ms
        break;
      case 72:                                      // Service Mode
        BlinkScore(0);                              // stop score blinking
        ShowLampPatterns(0);                        // stop lamp animations
        KillAllTimers();
        BallWatchdogTimer = 0;
        CheckReleaseTimer = 0;
        LampPattern = NoLamps;                      // Turn off all lamps
        ReleaseAllSolenoids();
        if (!QuerySwitch(73)) {                     // Up/Down switch pressed?
          WriteUpper("  TEST  MODE    ");
          WriteLower("                ");
          AppByte = 0;
          ActivateTimer(1000, 0, TT_Testmode);}
        else {
          Settings_Enter();}
        break;
      case 3:                                       // start game
        TT_InitGame();}}

This program only reacts to four switches. Switch 8 is the High Score Reset switch (at least for Sys7 and higher) and it activates the blanking signal when the switch is being pressed, which will turn off the displays, lights and all solenoids.

This feature is for protecting the lamps and displays of your pinball machine while reprogramming the Arduino. Basically you can reprogram your System 'on the fly', but when the reset kicks in it can happen that the lamps and displays light up shortly. This wont damage them, but they wont like it either and therefore I recommend to press 'High Score Reset' before initiating the software upload. Then everything is deactivated and comes up again when the new software is uploaded.

The next switch is activated when a ball arrives in the outhole, which is then shoved into the ball through.

Switch 72 is the Advance Button which will initiate the test or settings mode depending on the position of switch 73 Up/Down. Note that BlinkScore and ShowLampPatterns are called before the KillAllTimers command is being executed. This is related to what I've written in the previous section. Also be sure to call ReleaseAllSolenoids after using KillAllTimers, because it will also kill the release timers for the solenoids. After that the state of switch 73 is queried and depending on the result the Test Mode or the Game Settings are being called.

The next switch (3) is the game start button. It will call the InitGame routine which will do all the steps required to initialize a game and put a ball into the plunger lane. There's some quite complex stuff happening here, but for the moment it's enough for you to know that when the game is running and a switch is being activated the TT_GameMain routine is called. As you can see I have already inserted our drop target handling from the previous sections to the switches 49, 50 and 51 (they're for the Rollergames and probably different for your machine). That means you should be able to launch a ball and shoot the drop targets.

I hope you got a rough overview about how the APC software interface works. If you're interested in using it, please post your questions to one of the forums mentioned on the front project page. I'm willing to expand this documentation when there is a need, but at the moment most people seem to be interested in using the APC with PinMame and MPF, so I focus on this for the time being.

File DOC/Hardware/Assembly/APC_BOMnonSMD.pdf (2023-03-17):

APC_BOMnonSMD

Comment | Reference | Footprint | Mouser order number | Reichelt.de order number
Speakers | 10J2 | Molex4
Volume | 10J4 | Molex4
Diag Sw | 1J4 | Molex4
Display Segments 1 | 1J5 | Molex12
Display Strobes 2 | 1J6 | Molex9
Display Strobes 1 | 1J7 | Molex9
Special Sol Drivers | 2J12 | Molex9
Special Sol Triggers | 2J13 | Molex9
Switch Inputs | sys11_1J10 | Molex9 | | Only needed for Sys9 - Sys11
Solenoid Drivers 1 | sys11_1J11 | Molex9 | | Only needed for Sys9 - Sys11
Solenoid Drivers 2 | sys11_1J12 | Molex9 | | Only needed for Sys9 - Sys11
Lamp Rows | sys11_1J6 | Molex9 | | Only needed for Sys9 - Sys11
Lamp Strobes | sys11_1J7 | Molex9 | | Only needed for Sys9 - Sys11
Switch Drivers | sys11_1J8 | Molex9 | | Only needed for Sys9 - Sys11
Logic PWR/GND | sys7_1J2 | Molex9
Solenoid GND | sys7_2J10 | Molex9
Solenoid Drivers 1 | sys7_2J11 | Molex9 | | Only needed for Sys3 – Sys7
Switch Drivers | sys7_2J2 | Molex9 | | Only needed for Sys3 – Sys7
Switch Inputs | sys7_2J3 | Molex9 | | Only needed for Sys3 – Sys7
Lamp B+ | sys7_2J4 | Molex9
Lamp Strobes | sys7_2J5 | Molex9 | | Only needed for Sys3 – Sys7
Lamp GND | sys7_2J6 | Molex9
Lamp Rows | sys7_2J7 | Molex9 | | Only needed for Sys3 – Sys7
Solenoid Drivers 2 | sys7_2J9 | Molex9 | | Only needed for Sys3 – Sys7
CONN_36 | P4 | pin_array_18x2 | 538-10-89-7501 | SL 2X25G 2,54
Lisy_Jumper | P12 | pin_array_6x2 | use rest from above | use rest from above
Display Segments 2 | 1J8 | pin_array_13x2 | 538-10-89-7501 | SL 2X13G 2,54
Sys11_J21 | P11 | pin_array_8x2 | use rest from above | SL 2X10G 2,54
Raspberry_Pi | J1 | Socket_2x20 | 474-PRT-16763 | MPE 094-2-040
CONN_3X2 | P7 | Socket_3x2 | 571-215309-3 | MPE 094-2-006
SD_card | P8 | Socket_1x6 | 200-SLW11001TS | BL 1X10G 2,54
Ardu_pwr | P9 | PINHEAD1-4 | 538-22-30-3364 | SL 1X36G 2,54
CONN_2 | P6 | PINHEAD1-2 | use rest from above | use rest from above
CONN_6 | P1 | PINHEAD1-6 | use rest from above | use rest from above
CONN_7 | P2 | PINHEAD1-7 | use rest from above | use rest from above
CONN_8 | P5 | PINHEAD1-8 | use rest from above | use rest from above
CONN_2 | P13 | PINHEAD1-2 | use rest from above | use rest from above
Lisy_serial | P10 | PINHEAD1-5 | optional | optional
470u | C11 | Radial_D8_L13_P3.8 667-EEU-EB1V471B | RAD 470/35
100u | C2 | Radial_D5_L11_P2.5 710-860040272001 | RAD 100/25
1000u | C9 | Radial_D8_L13_P3.8 667-EEU-FR1C102L | RAD FR 1.000/16
IRL540 | | TO220 | 942-IRL540NPBF | IRL 540N
4,7K | RR1,RR7 | SIP9 | 652-4609X-1LF-4.7K | SIL 9-8 4,7K
18K | RR8 | SIP9 | 652-4609X-1LF-18K | SIL 9-8 18K
Shutdown | SW1 | Taster3301 | 653-B3F-1000 | TASTER 3301
74BCT760 | U19 | DIP-20 | 595-SN74BCT760N
TDA7496 | U21 | Multiwatt15V | 511-TDA7496

Use Mouser part number
538-26-48-1245

for all Molex connectors. These parts

have 24 pins and you can cut them as

required.
You need 204 pins if you want to be able to use the APC in all kinds of games from Sys3 to Sys11c.

If you want to use it only in Sys3-Sys7 OR Sys9-Sys11 games you can spare 6

connectors with each one having 9 pins.

That means 54 pins less which leads to
150 pins.

Q24,Q36,Q13,Q19,Q25,Q31,Q14, Q20,Q26,Q32,Q15,Q21,Q27,Q33, Q16,Q22,Q28,Q34,Q17,Q23,Q29, Q35,Q18,Q30

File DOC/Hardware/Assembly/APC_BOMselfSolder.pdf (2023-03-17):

APC_BOMnonSMD

Component | Reference | Footprint | Mouser order number
18K | RR8 | SIP9 | 652-4609X-1LF-18K
74BCT760 | U19 | DIP-20 | 595-SN74BCT760N
TDA7496 | U21 | Multiwatt15V | 511-TDA7496

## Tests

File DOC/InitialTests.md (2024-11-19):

# Initial tests

## Preparation

For these tests you need to have all components except of the Raspberry Pi populated and the APC SW installed.  
For the audio test take your sound file of choice, convert it with the [Audio Converter](https://github.com/AmokSolderer/APC/blob/master/DOC/UsefulSWtools.md), rename it to MUSIC.SND and copy it to an SD card which needs to be connected to P8 of the APC board. Of course you can skip this if you don't want to the APC to generate the sound.

## Switches and Displays

Put your board into your pinball machine, but only plug the connectors for Logic Power, switches and display: 

| Connector name | Number for System 3 - 7 | Number for System 9 + 11 |
|--|--|--|
| Logic Power | 1J2 | 1J17 |
| Switch Drivers | 2J2 | 1J8 |
| Switch Inputs | 2J3 | 1J10 |
| Diag_sw | 1J4 | 1J14 |
| Special Switches | 2J13 | 1J18 (if present) |
| Display Strobes 1 | 1J7 | 1J1 |
| Display Strobes 2 | 1J6 | 1J2 |
| Display Segments 1 | 1J5 | 1J3 |
| Display Segments 2 | - | 1J22 |

The [additional display cables](https://github.com/AmokSolderer/APC/blob/master/DOC/Prepare.md#system-7) of System 3 - 7 games must also be installed at this point.

Now power up your pinball machine. After some status messages your display should show 'USB CONTROL'. If you just see two brightly illuminated digits then turn off your machine immediately, because in this case your display strobing doesn't work.  
If you have a pre System11 machine with numerical displays or a System11 2x16 digit one you have to adjust the display setting to make it work correctly. A description how to do it is in the [settings section](https://github.com/AmokSolderer/APC/blob/master/DOC/Settings.md).

Even if your display works from the start you should enter the settings and browse through them to do a basic test of your switch circuitry.

Turn off your machine when the test is done.

## Solenoids

This step will test the solenoids. For this you have to connect the following connectors:

| Connector name | Number for System 3 - 7 | Number for System 9 + 11 |
|--|--|--|
| Solenoid GND | 2J10 | 1J13 |
| Solenoid Drivers 1 | 2J11 | 1J11 |
| Solenoid Drivers 2 | 2J9 | 1J12 |
| Special Sol Drivers | 2J12 | 1J19 |

If you hear the sound of an activating solenoid when turning on your machine then turn it off immediately, as it means that one of your solenoid drivers is stuck.  
If no solenoid is activated you can enter the 'System Settings' and set the 'Active Game' to 'Base Code'.  
Depending on your machine it might be possible that a solenoid is being periodically activated after you left the settings. This is not a problem as long as the solenoid is not turned on permanently and will probably be resolved after you have [set up the Base Code](https://github.com/AmokSolderer/APC/blob/master/DOC/SetUpBC.md) to your machine.

Turn off your machine when the test is done.

## Lamps and Audio

Now it's time for the lamps and the audio part.

| Connector name | Number for System 3 - 7 | Number for System 9 + 11 |
|--|--|--|
| Speakers | 10J2 | depends on sound config |
| Lamp B+ | 2J4 | 1J4 |
| Lamp GND | 2J6 | 1J5 |
| Lamp Strobes | 2J5 | 1J7 |
| Lamp Rows | 2J7 | 1J6 |

Turn on your machine. As you have an SD card plugged into the APC, the previous setting should have been stored and the Base Code should come up automatically. The attract mode of the base code has the lamps cycling from 1 to 64 which should be visible now.

Some words about audio:  
The APC offers a digital volume setting which let's you adjust the volume in the System Settings (Setting 6 'Speaker Volume'). This has the advantage of not having to use the old volume pots which are often bad after 40 years. However, the default volume setting is zero which means if you don't connect the volume connector 10J4 (1J16 for System11) you have to adjust the volume setting in order to have any sound.

## Using the Test Mode

The following description is about the test mode of the Base Code. That means you have to have 'Base Code' selected in the 'Active Game' setting of the '[System Settings](https://github.com/AmokSolderer/APC/blob/master/DOC/Settings.md#system-settings)' to perform this test.

Press the Advance button with Up/Down being in the down position to enter the test mode of the Base Code.  
The name of the current test is shown in the Display. For numerical displays the number of the test is shown in the Player 1 display. You can enter the test by pressing the game start button or proceed to the next test by pressing Advance again. The display, coil and single lamp tests are cycling automatically, the corresponding number is shown in the Player 4 display. This cycling can be stopped by the Up/Down button being in Down position.  
The following table shows the avaiable tests and their number which is shown for numerical displays.

| Test number | Test name |
|--|--|
| 1 | Display Test |
| 2 | Switch Edges |
| 3 | Coil Test |
| 4 | Single Lamp |
| 5 | All Lamps |
| 6 | Music Test |

Note that the switch test also shows numbers for the special solenoid switches (65 - 70). However, these switches are special and not part of the switch matrix.

## Next steps

If the tests are completed and your board is working properly you're ready to [run a game](https://github.com/AmokSolderer/APC/blob/master/DOC/RunGame.md)

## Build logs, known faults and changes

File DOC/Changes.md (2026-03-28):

# APC News and Changelog

## March 2026

### New SW Version V1.04

* You can now select up to 4 solenoids to have a recycle time of 250ms in the [game settings](https://github.com/AmokSolderer/APC/blob/master/DOC/Settings.md#game-settings-in-remote-control-mode). This comes in handy e.g. to prevent machine gunning of slingshots 
* Some finetuning of the sound files and PinMameExceptions for F-14 done
* [Debug logs](https://github.com/AmokSolderer/APC/blob/master/DOC/Problems.md#the-debug-mode) can now be written to USB
* Special Solenoids are not longer active during attract mode
* Exception rules for System 11 Whirlwind have been added. [Sound files for Whirlwind are also available](https://github.com/AmokSolderer/APC/blob/master/DOC/PinMame.md)
* Exception rules for System 6 Tri Zone have been added. [Sound files for Tri Zone are also available](https://github.com/AmokSolderer/APC/blob/master/DOC/PinMame.md)
* Native Pinbot code shows points >= 10M in highscore list if 4 Alpha + Credit display is installed
* Native Black Knight code shows points >= 10M in highscore list if 4 Alpha + Credit display is installed
* Ball Saver and alternative music implemented in native Black Knight code.

## June 2025

### New SW Version V1.03

* Stability fix in KillTimer() -> does only affect self written code with heavy timer use
* Bugfix -> MPF boot issue fixed by changing the reply to USB command 19 (get number of modern lights) to a two bit response
* New [System Setting 12](https://github.com/AmokSolderer/APC/blob/master/DOC/Settings.md#system-settings) 'Connect Startup' added. This is for MPF users who also use PinMame. With this setting enabled you can decide whether to boot Lisy/PinMame from the onboard PI or boot to 'USB control' mode by the state of the Up/Down switch. Hence, changing the 'Connect Type' setting is no longer necessary.
* Exception rules for System 6 Gorgar have been added. [Sound files for Gorgar are also available](https://github.com/AmokSolderer/APC/blob/master/DOC/PinMame.md)

## November 2024

### New SW Version V1.02

* The default name of music files has been changed from MUSIC.BIN to MUSIC.SND to be consistent with the APC audio files having .SND as a suffix. That means you might have to rename the MUSIC.BIN files of your SD card to MUSIC.SND
* A new option is available to replace the old (and sometimes annoying) [BG sound of old machines by MUSIC.SND](https://github.com/AmokSolderer/APC/blob/master/DOC/PinMameSound_3_7.md#adding-background-music). It can be activated with setting 7 in the [game settings](https://github.com/AmokSolderer/APC/blob/master/DOC/Settings.md#game-settings-in-remote-control-mode).
* A general ball saver is available. It can be activated with setting 5 in the [game settings](https://github.com/AmokSolderer/APC/blob/master/DOC/Settings.md#game-settings-in-remote-control-mode). There's [a list](https://github.com/AmokSolderer/APC/blob/master/DOC/PinMame.md#available-sounds) of supported machines. Look [here](https://github.com/AmokSolderer/APC/blob/master/DOC/PinMameExceptions.md#how-to-add-a-ball-saver) if it's not yet available for your machine.

## June 2024

### HW

* The package of the 74HCT273 ICs has been changed back to SOIC-20. They were TSSOP previously as the SOIC version was not available for some time

### New SW Version V1.01

* Bugfix -> Heavy use of timers could lead to system crashes
* Exception rules for System 11b Space Station have been added. [Sound files for Space Station are also available](https://github.com/AmokSolderer/APC/blob/master/DOC/PinMame.md)
* Exception rules for System 6 Time Warp have been added. [Sound files for Time Warp are also available](https://github.com/AmokSolderer/APC/blob/master/DOC/PinMame.md)
* Implementation of the new 3 ball multiball mode for [Pinbot](https://github.com/AmokSolderer/APC/blob/master/DOC/Pinbot.md) is complete

## December 2023

### HW

* C14 has been increased from 10µF to 22µF as some System11 machines had [startup issues](https://github.com/AmokSolderer/APC/blob/master/DOC/Problems.md)

### New SW Version V1.00

* General improvements for the Pinbot and Black Knight code added. Main feature is the new 3 ball multiball mode for [Pinbot](https://github.com/AmokSolderer/APC/blob/master/DOC/Pinbot.md)
* Exception rules for System 3 Disco Fever have been added. [Sound files for Disco Fever are also available](https://github.com/AmokSolderer/APC/blob/master/DOC/PinMame.md)
* Exception rules for System 6 Alien Poker have been added. [Sound files for Alien Poker are also available](https://github.com/AmokSolderer/APC/blob/master/DOC/PinMame.md)
* Bugfix -> if a sound/music file was invoked immediately after another, the first one was dropped regardless of the priority.
* Bugfix -> Controlling the original audio boards of System 3 - 6 games has been fixed.
* Support for single ball games added to BaseCode.
* Solenoid latches are updated every ms instead of on request which will revoke any accidental state change of solenoids. This can happen in heavily distorted environments when the distortion spikes are strong enough to trigger the latches. Distortion levels like these usually mean that something is wrong in your machine, e.g. a broken free-wheeling diode can cause this.
* System watchdog implemented. If the timer interrupt controlling the HW should not occur for 2s the system will restart.
* System 3 game adjustments implemented. You can now use the settings system of the APC to do the adjustments of System 3 games.
* New command StopAllBlinkLamps() implemented

### Misc

* Page for [installation frames](https://github.com/AmokSolderer/APC/blob/master/DOC/Frames.md) started. These make it easier to mount an APC in your backbox.
* PinMame Sound how-tos added to make it more clear what to do to let the APC play the original sounds

## March 2023

### New HW Version V3.1

* The packages of the LEDs have been changed to SMD.
* The fabrication files have been updated to let JLCPCB populate most of the non-SMD components also.
* An SMD adapter for SD cards has been added (P14).

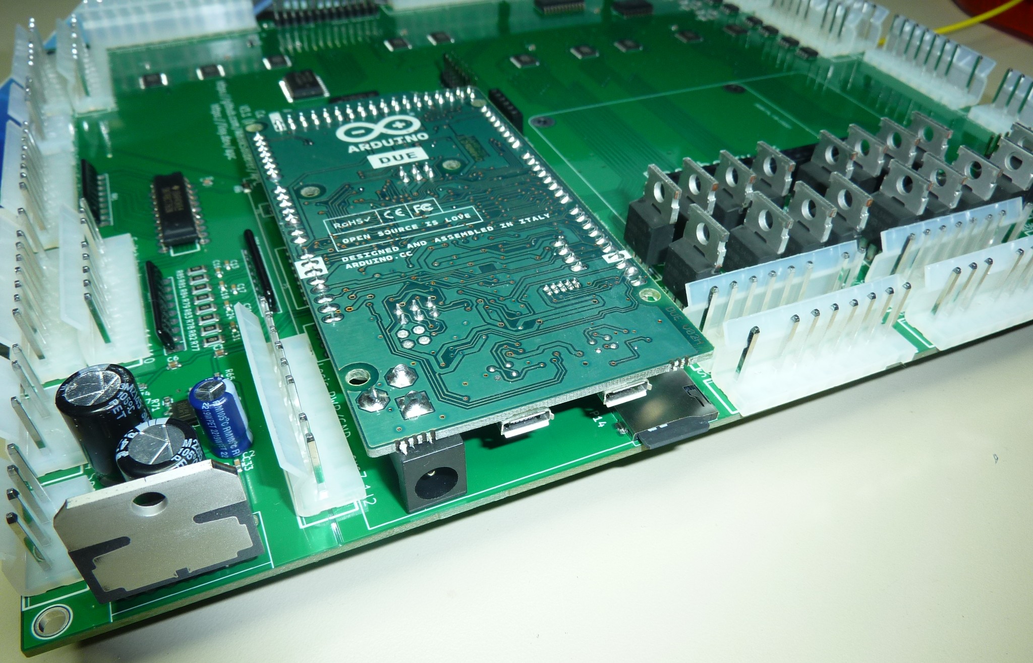
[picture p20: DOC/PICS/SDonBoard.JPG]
SD slot


The old connector for the self made adapter (P8) is still there, so you can decide which one you like more.

### New SW Version V0.31

* The ActivateSolenoid and ReleaseSolenoid commands can now handle recycle times for the 22 A-bank solenoids. Hence, you can prevent your slingshots from machine gunning without having to bend the switches.  
Check the [APC SW reference](https://github.com/AmokSolderer/APC/blob/master/DOC/Software/APC_SW_reference.pdf) to learn how to use it.
* The Pinbot and [Black Knight](https://github.com/AmokSolderer/APC/blob/master/DOC/BlackKnight.md) game SW has been improved

### Misc

* DOCs have been reworked, especially [section 1](https://github.com/AmokSolderer/APC#documentation-contents) "Building and setting up an APC".

## August 2022

### New SW Version V0.30

* Fixed a serious bug in USBcontrol. Depending on your settings this could lead to an Error 11 (or worse) at the end of a PinMame game when the flipper fingers are being disabled.
* Bugfix in USBcontrol. Serial debug (USB) interface can now be used when the 'Connection type' is set to 'OnBoard' and the debug mode in the 'System Settings' is set to on.

## July 2022

### New SW Version V0.23

* Bugfix in the AfterMusic(Sound) handling. When the StopPlayingMusic(Sound) command was immediately followed by PlayMusic(Sound) then the first AfterMusic(Sound) event was skipped.
* The types of AfterSound and AfterMusic have been changed from void (*)() to void (*)(byte). The Music/Sound routines call them with the argument = 0 when the Music/Sound file has run out.  
The purpose of this is to enable state machines that are initially called from the Music/Sound routines with the argument = 0 and can then recall themself after each step with the argument being set accordingly.
* The maximum number of effects that can be handled by the PlayFlashSequence command has been increased from 64 to 256.
* The StrobeLights() command has been reworked to make it more comfortable. You don't have to care about the StrobeLightsTimer any more. Just call Strobelights(Time) with Time > 2 to start lamp flickering with a period of (Time * 10ms). Call Strobelights(0) to turn off the flicker.
* Support for 2x16 character displays with additional numerical displays has been added.
* SW support for the [LED_expansion board](https://github.com/AmokSolderer/APC/blob/master/DOC/LEDexpBoard.md) has been upgraded. One change is that you can now install additional LEDs. Therefore the new system setting 'No of LEDs' has been added as [setting 8](https://github.com/AmokSolderer/APC/blob/master/DOC/Settings.md#system-settings). This might require resetting the system settings to the defaults, but it adds a lot of fun as you can see in [my Comet video](https://youtu.be/kLWVUdhSwfo).
* Exception rules for System 11 F-14 Tomcat have been added. Sound files for F-14 are also available (Thanks to Snux)
* A new setting 'none' has been added to the 'Backbox Lamps' setting in the system settings. This is for the ShowLampPatterns command to know which lamps not to include in lamp animations.
* The ShowLampPatterns command has been changed to support also games without any controlled lamps in the backbox. For this the Pattern array in LampPat has been changed from 7 to 8 entries. If your a game has the first column of lamps in the backbox you have to select 'column1' in the 'Backbox Lamps' seeting and add a zero after the duration. For games with the last row of lamps in the backbox change the setting to 'column8' and add a zero at the end of the pattern part of LampPat.
* Data East 2x16 displays are now supported. Therefore the entry 'Data East 2x16' has been added to the 'Display Type' setting in the system settings. As a side effect the numerical only displays move up one setting. Hence, if you have a System 3 - 9 type of display you have to re-adjust your display setting.
* Exception rules for System 9 Comet have been added. Sound files for Comet are also available

### Misc

* Due to the recent problems with the availability of the 74HCT273 at JLCPCB, I have split up the fabrication files section into two parts, one with the 74HCT273 in an [SOIC package](https://github.com/AmokSolderer/APC/blob/master/DOC/Hardware/APC_FabricationFiles_SOIC) and one with a [SSOP package](https://github.com/AmokSolderer/APC/tree/master/DOC/Hardware/APC_FabricationFiles_SSOP). Both folders contain all the required data to build a board, just the package of the 74HCT273 is different.
* The [4 Alpha + Credit display](https://github.com/AmokSolderer/APC/blob/master/DOC/Sys7Alpha.md) has been updated to support also System7 display cables with edge connectors.
* My [APC Black Knight](https://github.com/AmokSolderer/APC/blob/master/DOC/BlackKnight.md) game code has been updated.
* My Pinbot code has also improved a lot, but I don't have an own section for it yet.
* A new [Known issues](https://github.com/AmokSolderer/APC#known-issues) section has been added to point out problems and limits of the APC.

## July 2021

I got a notification from Mouser that the TDA7496 audio amplifier IC won't be produced any longer.

At the moment I don't have the time to select a new amplifier IC, change the board design and do the necessary tests. I might do it in the future if the IC is not available any more.  
That means you should try to get these ICs before you order any boards.

## June 2021

### New SW Version V0.22

* A new exception handling system has been implemented. This makes it easier to program machine specific changes while using PinMame. Take a look at the [PinMameExceptions](https://github.com/AmokSolderer/APC/blob/master/DOC/PinMameExceptions.md) page for details
* Exception rules for System 7 Pharaoh have been added. Sound files for Pharaoh are also available (Thanks to Grangeomatic)
* Exception rules for System 6 Firepower have been added. Sound files for Firepower are also available (Thanks to Matiou)
* Support for 6 digit numerical displays (System3 - 6) has been added
* Support for System 3 - 6 sound boards as well as System 11 audio boards has been added
* The Pinbot exceptions have been changed to handle the looping music scores correctly
* Exception rules for Rollergames have been added, but there seems to be a problem with PinMame sending erroneous music commands. This happens only during a game, the music test works perfectly. This issue is still unsolved, so any help is welcome.

### Misc

* There's a new section [If things don't work](https://github.com/AmokSolderer/APC/blob/master/DOC/Problems.md) in case you encounter a problem
* The 74HCT273 ICs from Nexperia have run out of stock at JLCPCB quite some time ago and they don't seem to reorder them. Therefore the type of this IC has been changed to the Texas Instruments part.

## January 2021

The APC 3.0 board has most components populated by the board manufacturer. As this reduces the probability of soldering errors significantly, the set up and test procedures could be made a lot easier.

### New SW Version V0.21

The Base Code set up can now be done in the Game Settings, without having to do any code changes.

### Misc

The setup and testing procedures have been changed in the DOCs. Some Lisy specific documentation has been added.

## December 2020

APC 3.0 is released. See my [APC 3 video](https://www.youtube.com/watch?v=4EgOTJyxMXo) to get an impression what has changed.

### New HW Version V3.0

* The Lisy_Mini board is no longer needed to run Lisy (for PinMame or MPF) as the Raspberry Pi has been added to the APC board itself. Note that the 'Connect Type' setting must be set to 'On Board' for the on board Pi to work. This has been done to still be able to ignore the on board Pi and control the APC from the USB port if needed.
* The Hardware Extensions Interface has been upgraded to have 5V logic level also at the select pins. Furthermore the data lines can now be latched which makes it possible to control System7 audio boards without having to use additional HW.
* The board has been reworked to use SMD ICs where possible and move all components to the top side. This makes it possible to populate the board at the board manufacturers. All necessary fabrication files can be found in the [fabrication files folder](https://github.com/AmokSolderer/APC/blob/master/DOC/Hardware/APC_FabricationFiles).

### New SW Version V0.20

* Display blanking for the various display types is now handled by SW which makes jumper JP1 and the resistor arrays RR2 - RR5 obsolete. This does also work for APC 2.x boards.
* The functionality of pre System11 sound boards has been modelled. This make it easier to use the PinMame sound of System 3 - 9 machines. For Systems 3 - 7 it is also possible to use the original audio boards.
* Support for System7 displays has been added.
* USBcontrol mode has been renamed to Remote Control Mode as the APC 3 can also be controlled by the on board Pi.

### Misc

* Sound files for Black Knight and Jungle Lord are available on request. They can be used with PinMame or as a basis for own games.
* A summary of the [Documentation contents](https://github.com/AmokSolderer/APC/blob/master#documentation-contents) has been added at the end of the main page to provide a better overview about the documentation.

## April 2020

PinMame is working.

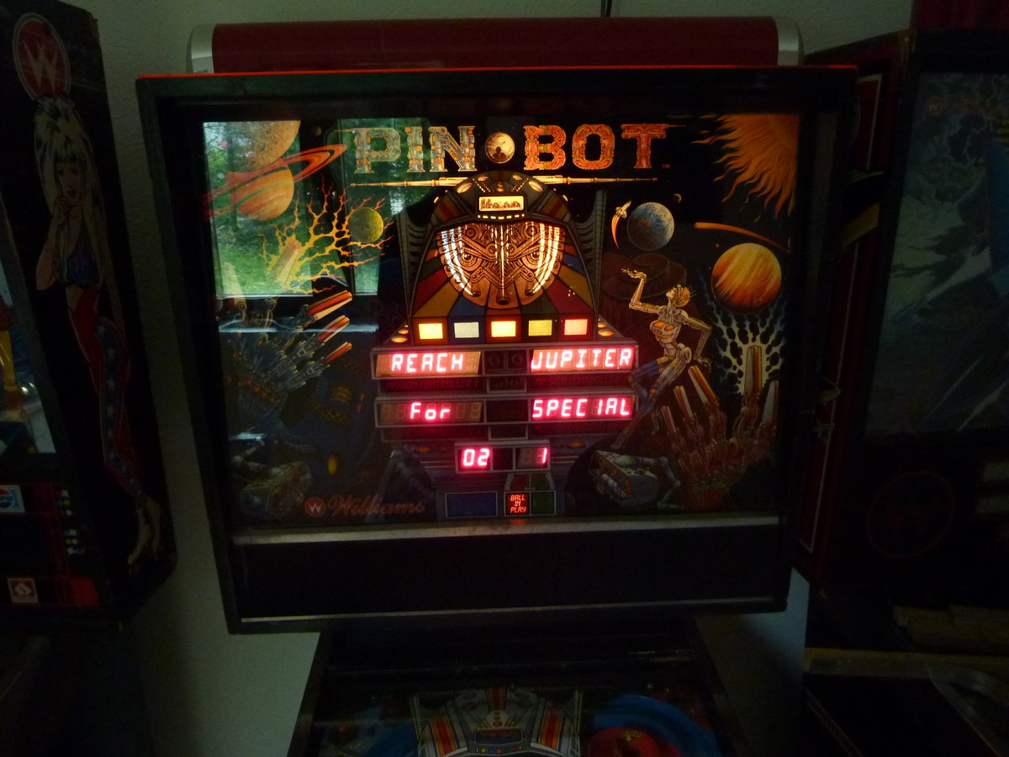
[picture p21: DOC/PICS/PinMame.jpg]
PinMame


Watch the

[Lisy, APC and PinMame](https://youtu.be/cXrh-XPqCKw)

video to see my old Pinbot under PinMame control.

There's still some work to be done, but with this setup you can do much more than just playing the original game. See my [PinMame page](https://github.com/AmokSolderer/APC/blob/master/DOC/PinMame.md) for details.

### New SW Version V0.13

The SW comes up in USBcontrol mode now instead of the BaseCode. The reason for this is that some people are using the APC with MPF, but without having any displays connected to it. This makes it quite cumbersome to change the game mode, so the default was changed accordingly.

Some changes have been implemented for PinMame support, especially concerning the sound handling.

The Black Knight game SW has been upgraded to implement more sounds and effects. Contact me if you're interested in getting the corresponding sound files.

## Sep 2019

It has required some additional changes in the SW to make the sound work completely with MPF, but now it's done.
That means the APC is all set for MPF, as you can see in the following video:

[MPF runs APC](https://www.youtube.com/watch?v=w4Po8OE5Zkw)

It's not a cineastic masterpiece (again) but it shows that everything works now. Sorry for the slight display flicker - it's just caused by my camera, in reality the displays look just fine.

### New SW Version V0.12

Some changes in the USBcontrol.ino to make the sound commands fully compliant to MPF.
You can find my MPF configs in DOC/Software/MPF. I don't know whether they qualify more as a good or a bad example, but they might be helpful anyway.

## Aug 2019

After some changes in the USB protocol the displays are now also working with MPF.
Snux has already shown it all working in his famous F-14

[F-14 game video](https://www.youtube.com/watch?time_continue=1&v=XAQ0JEPhWv4)

The only thing that hasn't been completely tested yet is the sound. It works when you're sending the necessary USB commands with a terminal program - I tried that. So from the APC point of view it should be OK.

### New SW Version V0.11

The new SW Version is V0.11 which affects only the USBcontrol.ino and changes the display numbering to be consistent with MPF.

### New HW Version V2.4

Apparently Williams changed the ground wiring of the direct switches for the special solenoids from Sys11 to Sys11a. Since Sys11a these switches have to get their ground from the pins 6 and 7 of 1J18. Unfortunately they didn't change it in the schematics where they're still marked as NC. Many thanks to Snux for pointing this out.

This required a new HW release which has both pins connected to ground and I used this opportunity to change the supply of the old volume pot to 5V. Before this you could theoretically damage your audio amplifier by turning up the digital volume control with the volume pot still connected. Even though this is unlikely and not allowed as stated in the Wiki, I wanted to eliminate any risk for damaging the HW. However the volumes will still add up when the the connector is not diconnected and you might blow you speakers (or your ears).

## July 2019

Snux has successfully made the attract mode of his 'F-14 Second Sortie' work with the APC:

[F-14 attract mode video](https://www.youtube.com/embed/XlqPyIdEk2k)

Don't be suprised about the boring display. As the new display protocol is not yet implemented in MPF the display cannot be controlled yet.

### Change in the BOM

When Snux used his LED lamp tester it became obvious that there is some 'crosstalk' between the lamp columns. That means if a lamp is turned on, it's counterpart in the previous lamp row shows a weak glow.

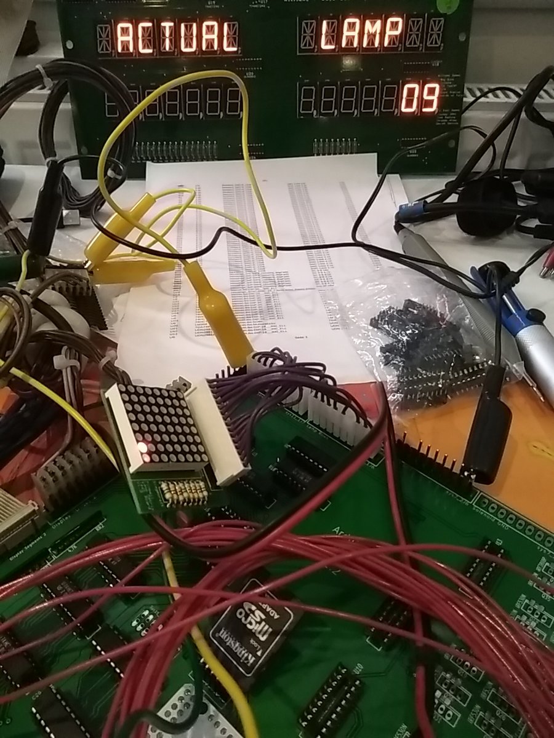
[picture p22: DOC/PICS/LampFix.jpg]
LampFix


It's much less obvious with the normal light bulbs, but I wanted to fix it anyway. For this reason the values of the resistors R1 - R16 have been changed to speed up the column driver.

### New SW Version V0.10

* SW version number will now be shown during startup.
* The lamp timing has been changed slightly to suppress the 'crosstalk' between the lamp columns (see above)
* The USB display protocol has been updated as agreed with the Mini Lisy and MPF developers

## June 2019

First experiments with [Lisy Mini](https://lisy.dev/lisy_mini.html) which is used to run PinMame and control the APC via USB.

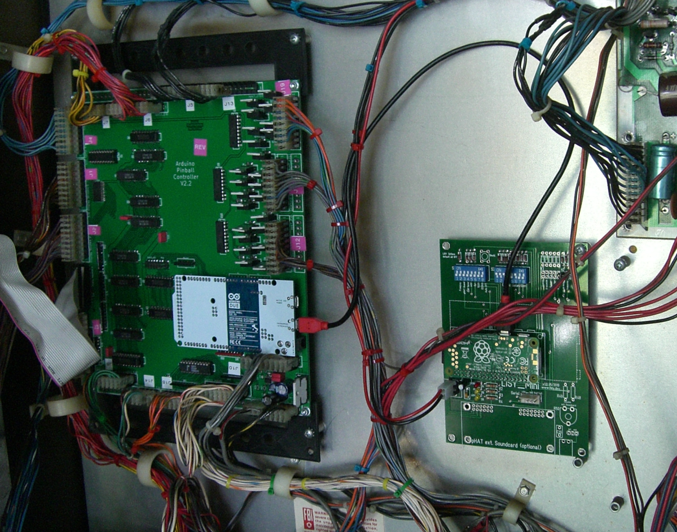
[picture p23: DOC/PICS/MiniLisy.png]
Pic Mini Lisy


Attract mode of a Comet (System9) is already working. The display protocol still needs some work, but we're going to do that together with the MPF guys.

And I wish my backboxes were so clean and tidy.

### New HW Version V2.3

The pre Sys11 machines need an inverted blanking signal for their displays. In order to generate this signal an additional transistor Q8 and a base resistor R88 have been added. Furthermore the 'Display Segments 1' connector has been enlarged from 9 to 12 pins. System9 can use this connector directly, Sys 3-6 machines only require the Blanking_N pin and Sys7 users have to connect the comma pins additionally.

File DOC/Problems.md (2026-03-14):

# If things don't work

## APC doesn't boot

On some System 9 and 11 machines the APC doesn't boot sometimes. Usually it is enough to powercycle your machine or to press the reset button of the Arduino DUE to make it work.  
If it happens frequently then you could swap C14 from a 10µF to a 22µF capacitor. Boards fabricated after [December 2023](https://github.com/AmokSolderer/APC/blob/master/DOC/Changes.md#hw-1) should already have this fix.

## The debug mode

There's a main debug mode available which can be activated in the [System Settings](https://github.com/AmokSolderer/APC/blob/master/DOC/Settings.md#system-settings) or by changing

    #define DebugState 0    // set this value to 2 and remove SD card for USB debug log

at the top of the APC.ino file. In the latter case you have to recompile the SW afterwards and upload it again to the Arduino. If greater that zero, this definition will overrule the selected value in the System Settings.

A setting different from zero will activate a serial interface at the USB (programming) port of the DUE. You can use the serial monitor of your Arduino IDE or any serial terminal program to display the messages.  
Note that you cannot control your APC via USB (e.g. with MPF) while the USB debug mode is enabled. It might also slow down your system, so only turn it on for as long as it's needed. 

* A setting of 1 will display critical error messages and halt the system afterwards, but you're free to use this interface from your own code with e.g. the Serial.print command

* Setting this to 2 is useful if you have pure numerical displays and you want to see the settings menus or error messages in full text. After startup the APC will then list all settings in full text. If you enter the settings, then the APC will show the name and value of the current setting, just like you'd see them on an alphanumerical display. Also file not found errors for audio files will show up here.

## Sound stuttering

If your sound has unregular lags and stutters sometimes then it's most probably an issue with your SD card.
 
The first thing to try is to format your card with a special SD-card formatting tool like the one from the SD Association (sdcard.org) which can improve the time your SD card needs to open a file. This can be crucial especially for pre System11 machines as their sound sequences usually consist of lot's of single sounds. Each of these sounds requires a new file on the card to be opened and if your card cannot open the files fast enough than the sounds just start to stutter.

If this doesn't work then try a different SD card. I had several SD cards of the same brand, but for some reason one of these cards just produced sound lags on my Pinbot, even though I had it formatted with the formatting tool. After I replaced the card with one of it's siblings everything worked fine.

However, some sound sequences might just be too challenging for your SD cards.  
The solution is to record the whole sequence into one single sound file and to play this with a high priority. This requires only one file to be opened for the whole sequence and the high priority blocks all subsequent sound commands from PinMame as long as the file is being played.

## Damaged Arduino clone

If you're using a chinese clone of the Arduino DUE which just stopped working and draws a huge current instead, then it's most probably a blown buck converter IC.  
You can check this by supplying your DUE on the bench (without the APC board) with 5V. Then check the temperature of the marked IC.

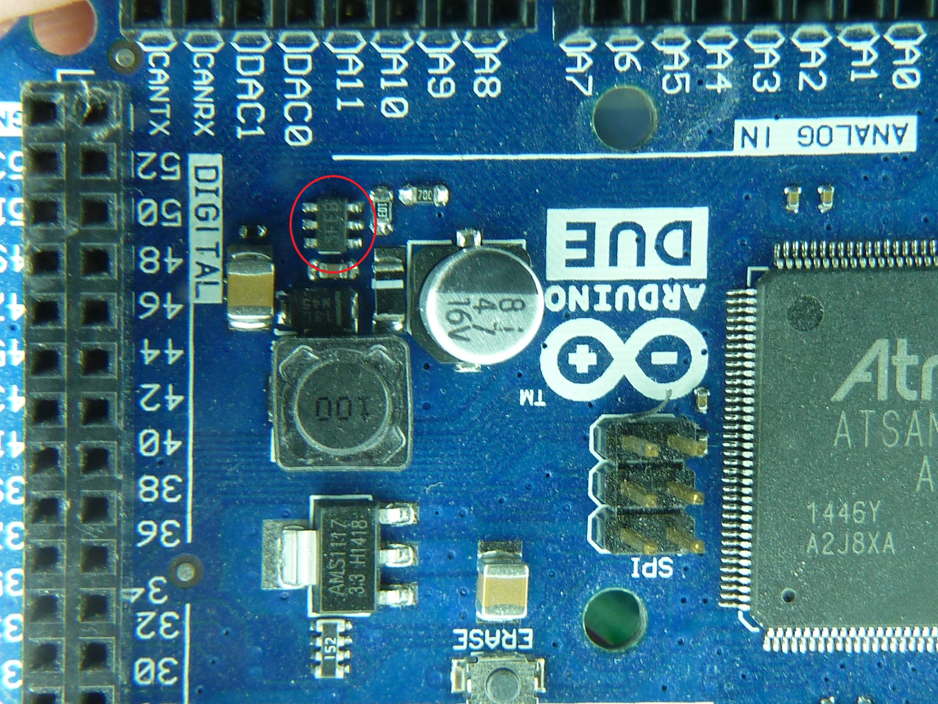
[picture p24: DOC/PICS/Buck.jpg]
Buck


If the IC gets hot then it's damaged. The good thing is that you don't need this IC when using the DUE with the APC, so you can just remove it and your system should run fine again.

## PinMame game doesn't start

If the displays are working, but the game doesn't start, then the LEDs on the APC board can help you to find the problem.  
The meaning of the LEDs is:

|Color|Meaning|
|--|--|
|Yellow|Lisy has been started on the Raspi and is now trying to contact the Arduino DUE|
|Green|Communication between Raspi and DUE has been established|
|Red|Communication has failed|

* After the machine has been switched on, all LEDs are off while the Raspi is booting. If you have alphanumeric displays they should show 'Booting Lisy'. If they show 'USB control instead, read the 'red LED' part below. 
* When the Raspi has finished booting, the yellow LED will be lit to show that it is trying to reach the DUE. If the yellow LED does not light up, then something is wrong with your Raspberry Pi. There is an LED on the Pi which will flicker while the Pi is reading data from the SD card (e.g. while booting). If this LED stays dark, check your SD card and be sure to have Lisy installed correctly. Note that [Lisy Embedded](https://lisy.dev/lisy_embedded.html) will only work on the correct hardware.
* If the green LED is lit, the communication works. If the game still doesn't work correctly, check the [settings for PinMame use](https://github.com/AmokSolderer/APC/blob/master/DOC/RunGame.md#pinmame) like the PinMame game number.
* A red LED shows that the communication has failed. Check that 'Active game' (setting 1  of the System settings) is set to 'Remote Control' and 'Connect Type' (setting 4) is set to 'On board'. This will select the Raspi located on the APC board for communication.  

## Fixing a dead APC

If neither switches, lamps, solenoids nor displays work any more, you might have a damaged data bus on your APC. In this case the green LED will still be lit after startup when you're in 'Remote Control' game mode and have a Raspberry Pi on board, but except of the sound nothing will work. Pre System11 displays will probably show all zeros and BK2K style displays will look like this:

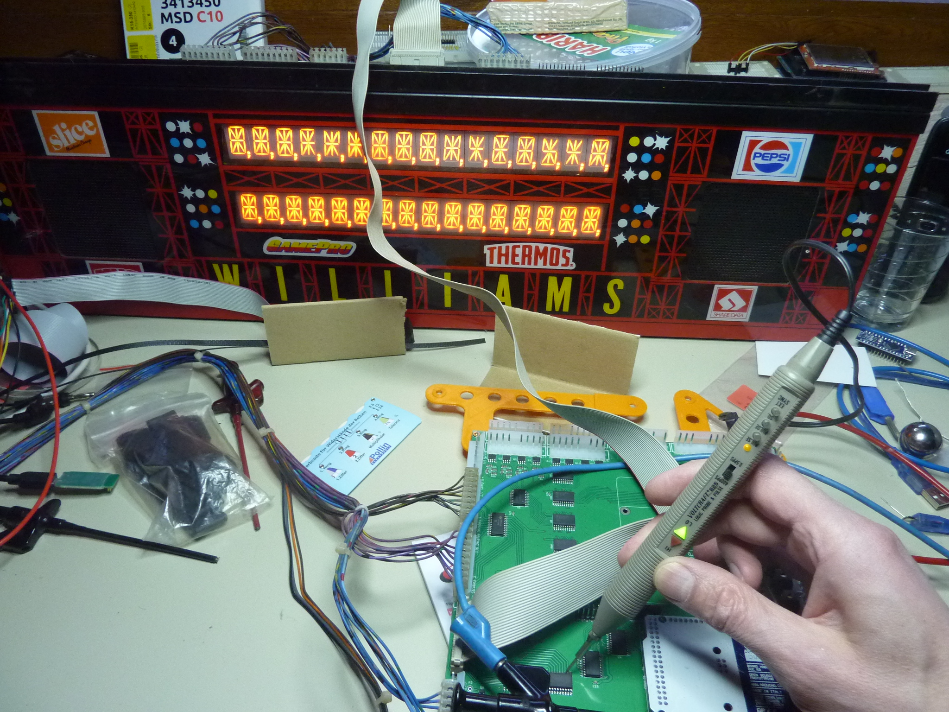
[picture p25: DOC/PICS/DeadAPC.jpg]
DeadAPC


If you have none of the display types mentioned above, they'll just be dead and you have to use a logic probe or an oscilloscope to check the display strobe signals (Sys11_1J1 and Sys11_1J2) for activity. If those signals are pulsing, you should check the pins (12 to 19) of U2. If they're static (like in the picture) your data bus is dead.  
You should now check the input signals (pins 2 to 9) of U2. However, these are 3.3V signals so be sure that your logic probe can handle those or use an oscilloscope. If the input signals are also static you should check your Arduino DUE, otherwise you can locate the problem as follows:  
The APC uses an 8 bit data bus to control most of the HW. If this bus is dead then this is most probably caused because one of the latches addressed by this bus is damaged and shorting the signals of the bus to 5V or GND.  
Finding the damaged latch can be tricky as they're all connected in parallel, but the most likely candidate is the switch driver latch U23. This latch is providing the signals of the switch row and can therefore be damaged by high voltages being shorted to the switch matrix.  
You can remove the IC quite easily with two soldering irons. If the APC comes to live again with the IC removed, you have found your problem, but be sure to fix the short in your switch matrix before installing a new IC.

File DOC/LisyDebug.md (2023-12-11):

# Controlling Lisy

This page covers just the APC relevant basics. In some cases it might be necessary to read the corresponding chapters in the [Lisy manual](https://lisy.dev/documentation.html).

Note that the following debug features are only available while using the normal Lisy version. Lisy Embedded does not include these features.

The basic mode of Lisy is selected by the Lisy_Jumpers P12 which are depicted below.

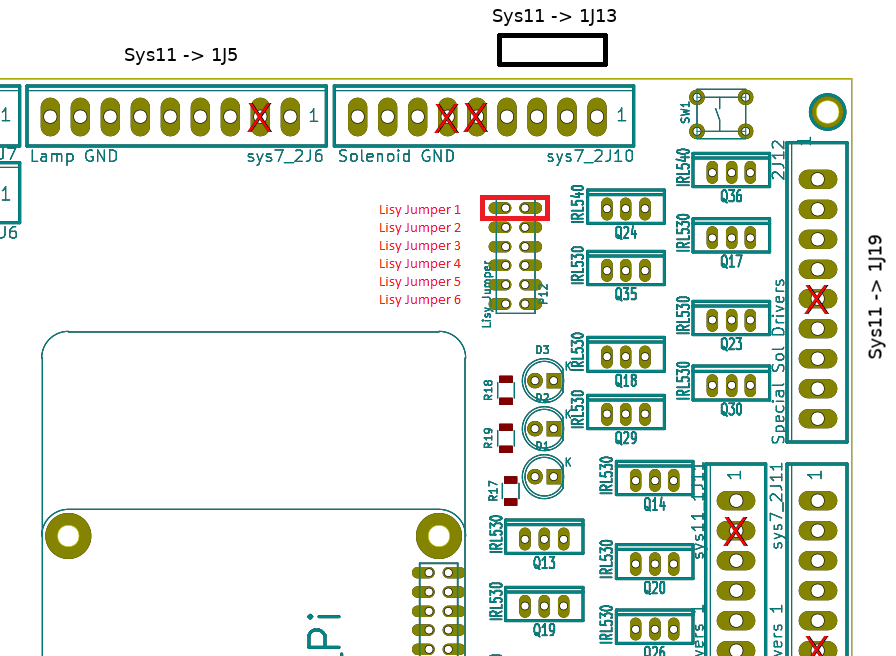
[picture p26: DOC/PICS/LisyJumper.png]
Lisy Jumper


|Jumper|Function|Comment|
|--|--|--|
|1|No Autostart|Lisy won't start PinMame after booting up|
|2|Hotspot Mode|Lisy will start a WiFi hotspot instead of using the local Wifi|
|3|Debug Mode|Writes a debug log|
|4|Lisy Control|Starts the Lisy Webserver|
|5|Not used||
|6|Not used||

## Setting up WiFi

All the features described below do require a working WiFi which means you have to put a WiFi capable Raspberry Pi (Zero or Pi3) on your APC board.

To set up WiFi you have to find the following file on your Lisy SD-card

    /lisy/lisy/ wpa_supplicant.conf
    
and change the settings for 'country', 'ssid' and 'psk' to those of your wireless network.

For more information about Lisy and WiFi, please read the 'Wireless config' section in the Lisy manual.

## Updating Lisy

With WiFi working you can use the incremental update function for minor updates instead of having to write a new Lisy-image to the SD card. 

With WiFi set-up and the system being switched off, connect the jumper 4 (Lisy Control) and power up your machine.  
After booting up, Lisy will try to connect to your WiFi. If the connection is successful, the obtained IP address is shown in the pinball displays.  
Enter this IP address into your browser to connect to the LisyControl webpage where you can initiate an update.

## Lisy Debug Mode

Lisy comes with a build-in Debug Mode which writes a debug log to the SD card of the Raspberry Pi when activated.  
Before you start the Debug mode you have to specify what kind of debug information you want to have logged. To do this, enter the 'Game Settings' of the 'Remote Control' Mode and change the 'Lisy Debug' setting accordingly.  
The value for 'Lisy Debug' can be derived from the following table.

|Debug Option|Value|
|--|--|
|Displays|1|
|Switches|2|
|Lamps|4|
|Solenoids|8|
|Sound|16|

If you want to log more than one option you have to add the respective values. For example, if you want to log the events for switches and solenoids you have to select 10 here.  
Don't forget to select 'Exit Settings' to store your changes to the APC's SD card.

To start the Debug Mode, turn off your machine and set Lisy jumper 3 before turning it back on. The system will now log the selected debug information, but this doesn't mean that it is immediately stored on Lisy's SD card. You should therefore not just turn your pinball machine off after your debug session, but press the Shutdown Switch SW1 which will initiate a controlled shutdown of Lisy. After that you can turn off your machine and remove the SD card of the Raspberry Pi.

The log file is located in the /lisy/lisy_m/debug folder.

## Remote debug Mode

Lisy can also be controlled remotely via WiFi. In this mode it'll just print all information directly into your shell, including the debug log. Hence, you don't have to bother with removing the SD card any more, since all the required information is already on your screen.

If you have set-up the WiFi configuration of your Lisy system, you can use the Remote Debug Mode as follows:

With your pinball machine switched off, connect the jumpers 1 (No Autostart) and 3 (Debug Mode).  
After you've turned on the power, wait for the yellow LED to light up. Now Lisy has booted and is waiting for instructions.  
First you have to obtain the IP address of Lisy in your WiFi network. Then open up a shell on your PC and use this address to connect to Lisy via ssh: 
 
    ssh pi@IP-address

Log into the system by using lisy80 as the password.  
Now it depends whether you're using the Pi on an APC 3 or on a Lisy_Mini board. In case of the APC 3 you have to use

    ./run_lisy_apc
    
to start PinMame and with a Lisy_Mini board it's

    ./run_lisy_mini
    
These commands will run Lisy and print a complete log into your shell.

### Remote mode and Lisy updates

The run_lisy_apc and run_lisy_mini commands are not automatically updated with your Lisy system when the update is done via Lisy Control. That means you have to change these scripts manually.  
Let's use the run_lisy_apc script as an example. Normally it looks as follows:

    sudo ./lisy/xpinmame.vid_lisy -nosound -skip_disclaimer -skip_gameinfo -nvram_directory /pinmame/nvram -rp /boot/lisy/lisy_m/roms lisy_apc
    #sudo /usr/local/bin/lisy -nosound -skip_disclaimer -skip_gameinfo -nvram_directory /pinmame/nvram -rp /boot/lisy/lisy_m/roms lisy_apc
    
To activate the Lisy update you just have to move the comment sign from the second to the first line and you're done.  
Note that you have to issue an rw command first in order to set Lisy into read/write mode.

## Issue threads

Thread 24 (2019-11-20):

System 7 display

patzik, 2019-11-20:
Not so much an issue, more a request.

I found your design of the replacement for the score display. I have a system 9 machine (comet) with 2 broken displays and would love to build a replacement for this. Would this display also work on this machine? Now for the request, my machine had the driver board with the edge connectors, could you PLEASE make a version of the driver board with this connection?
If there is anything I can do, just let me know, I don't know what design software you use, but I am familiar with eagle so I might be able to change the design if I had the source files.

patzik, 2019-11-20:
Also, what kind of led segment displays did you use and where did you get them?

AmokSolderer, 2019-11-21:
The Sys7Alpha displays on this page are only for use with the Arduino Pinball Controller. They would work in a Comet, but only with the APC installed.
The original System9 hardware cannot use these displays as they're alphanumeric and they use the System11 connectors (that's why there are no edge connectors).

If you just want to replace the displays and not the controller you would need something like this [http://baumfalk.net/Displays/sys7_en.html](url).
This is a design I did some 15 years ago, not sure whether I'm able to find the old design files.

patzik, 2019-11-21:
Yeah, I noticed the alpa displays and the 'extra' connector today, but the link you posted looks promising! I can't etch pcb's so I'm unable to use those files, but looks like that's exactly what I need. I would really appreciate it if you can look for those files, it would be great if I can make some gerbers and have those boards made. I might look into the APC in the future, but I first want to get the displays working so my sons can play with their friends...

patzik, 2019-11-22:
I tried all day to import the pdf's into eagle but the result is not something I can work with. The best thing would be the source files so I can also adjust the display boards if needed for other 7 segment display elements, maybe the cheaper Chinese ones.

I have my fingers crossed ;-)

AmokSolderer, 2019-11-24:
I found some old design files, but they don't work with my actual KiCad version any more. Looks like I have to install an older version to open those files.
This is going to take a while I'm afraid.

patzik, 2019-11-26:
Great that you found some of the files!
Could you send me the design files or put them on the GitHub, I can install an older version of kicad or convert the files and see what I can do with them.

AmokSolderer, 2019-12-02:
The files are a mess. They have been migrated some time ago from a 15 year old Eagle version to KiCad 3. With a bit of rework I was now able to import them in KiCad 4. The Layout looks OK, just the board text is still missing. The schematic is still messy, but hopefully good enough to move forward to KiCad 5 for the final overhaul.
You can take a look in the V00.13 branch on GitHub. The Archive is in APC/DOC/Hardware/Sys7_Display, but I strongly recommend to wait until I had time to fix it.

patzik, 2019-12-03:
I took a quick look, and I see what you mean with the schematic. I'd like to help, unfortunately I use eagle, so I'm not that familiar with kicad (although I have it installed). The board looks fine, so I guess it would be possible to generate gerbers from this or would that run into problems?
But the kingbright led's are hard to get here and ordering them from the us would be costly.
I found some similar led's in China (less than 0.40 euro each), and they should work just the same, but they have a different pinout, maybe you could make 2 display boards for the different led's? Here's a picture of their details.

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

Thank you for looking into this, really appreciate it!

patzik, 2019-12-04:
I was able to open the files with 4.0.7 and looks much better now, version 5 of kicad gives me noting but trouble :-(
Still having problems with switching from eagle to kicad, it's just so different, I don't understand how kicad works, so my hopes are one you...

AmokSolderer, 2019-12-06:
I'm sorry, but I just don't have enough time to support different display types. Apparently it's going to be more than enough trouble to bring my old designs to KiCad5.

It would be a different story if you'd be able to find a display having a package width of less than 20mm. That's because the current displays are a bit too wide and need to be grinded down to the correct width which is kinda cumbersome.

patzik, 2019-12-06:
I totally understand, and appreciate the time you put into this. I have looked for displays that are less than 20mm but can only find the 20mm ones. Do the 'commercial' reproduction displays also file down the segments or are they available in a narrower size?

AmokSolderer, 2019-12-07:
They are available in China, but you have to order at least 1000 pcs.

patzik, 2019-12-10:
Yes I see that the segments can be 19.05mm wide. I Can't find any dip packages in that size, what do you have any info on the ones that are available? I did however find smd packages that should work perfectly, they are also thinner so that should also help with 'distance between the display and the backglass. Did you look into these?
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

AmokSolderer, 2019-12-11:
> Did you look into these?
No, I didn't actively look for a replacement for a long time. The Kingbright displays never failed me and grinding them down a bit is a bit cumbersome, but not that much work especially if you only have to do it every now and then.
The only thing that's bugging me is that I also did a design for a System11c display (2x16 alphanumeric), but never realized it because it requires displays with even less width. Therefore I'd be interested what kind of display you found and whether it is available as an alphanumeric type also.

I do now that a display called 8018SBO is being used for some pinball displays. Search Google for it and you will find some chinese pages offering them in quantities of 1000+. There's also a numerical version called 8015SBB.

patzik, 2019-12-13:
They are ACSC08-51SEKWA (same brand), I found these here.
https://nl.mouser.com/Search/Refine?Keyword=ACSC08
But they are also available in China
https://nl.aliexpress.com/item/32715904139.html?spm=a2g0s.8937460.0.0.399e2e0eRfcL0o

As far as I can see they are not available in a 16 segment version.

Looking at the footprint of the ones I mentioned earlier (the dip version) and these, i guess it would be possible to design a board that can accommodate both if you use longer pads with the through hole. (just and idea)
I find kicad hard to use, do you know if it's possible to convert from kicad to eagle?

AmokSolderer, 2019-12-16:
Are you located in the Netherlands? Then you might want to try Reichelt.de, as they have quite good prices. [https://www.reichelt.de/7-segment-anzeige-rot-20-3mm-gem-anode-sa-08-11-rt-p31575.html?&trstct=pol_0](url)

I also found the old Eagle files and put them to GitHub.

patzik, 2019-12-16:
I am indeed from NL, and those are indeed reasonable prices so that might be an option.
How did you 'file down' the digits to make them narrower?
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
AmokSolderer, 2020-05-11:
No, they can't all be bad. If you're sure that you have the right ICs then may be your pinball MPU is not doing what you're expecting?
I think to check that you should unplug the BCD-IN1 connector and apply some BCD code manually. This way you can check your 4511 devices without any interference from your MPU.

BTW, I doubt that any of your 7316 is bad also. No device leaves the fab untested and you're not the first one having problems to solder SO-8 packages.

patzik, 2020-05-11:
The original display is working fine (although 2 displays are outgassed), so I assume the MPU is also working fine. I connected a normal led with a resistor to the outputs of the 4511's and I can see the led although continuously lit changing brightness just a bit when the segment is turned on/off so it looks to be working but the low state is just not 0v. I will try to find new 4511's tomorrow, and see if that makes a change.
As far as the 7316's, I don't think it's my soldering unfortunately. I have soldered many projects with tqfp packages and 0603 parts by hand, so compared to these the 7316 is huge ;-)

patzik, 2020-05-12:
Well, made some progress today. Luckily there is an electronics store really close to my home with a huge assortment. They had 4511's from different brands and I bought a set of motorola's and a set of philips. The motorola's didn't light all segments, it was more the opposite, maybe one segment lit up and didn't go out so no success. The philips however worked! All segments work perfectly now. I can't really explain this, and am really curious why some brands work and some brands don't, but I'm happy I found a working set.
Only one thing left to fix now, because I still have a problem with some digit's not lighting up. Seems the irf7316's are also hit and miss. I have gotten to the point that all digits except digit one on display 1 and 3 are working. I have changed the related 7316 (Q1) about 5 times now and can't seem to get it to work. Strangely enough there is a voltage on the common pin of the digit, so you would think it would work. I tried different displays but this made no difference. The outputs are 5+6 and 7+8, somehow if I short the 2 pairs the 1'st digit does light up but I don't think it would display correctly (only tried test mode where all numbers are the same).
I also swapped around the 4050's but this also made no difference and the contact on the edge connector is good and the digit does work with the original displays so seems like another strange problem...
Will try some more options, and hope to get it to work.
I designed a 'cover' for the displays where only the segments and the 2 komma's are visible, works out really nice. Have to finetune it just a bit, are you interested in adding these to the GitHub when finished?

patzik, 2020-05-12:
Success!!

I still don't know why and how, but swapping some more with the irf7316 finally ended up in a working combination. I'm 100% sure it's not the soldering and will do some more 'troubleshooting' with the 2nd board, as it is build already, and I'm very curious about the cause. But not touching this board again, this one stays in!
Thank you so much for your help, hope I can return the favour someday. Oh and If you like to add the stl for the 'cover' just let me know.
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

AmokSolderer, 2020-05-15:
That's very strange. I've used dozens of IRF devices over the years (the APC uses them also) and never had a bad one.
Probably your cover does only fit on your special display elemnts or do you think it would fit on the Reichelt ones also?

patzik, 2020-05-17:
The size of the Reichelt ones are the same so it should also fit the same. I am not sure if the cutouts for the segments and komma are at the exact same place though, and I don't have one of those elements to testfit. If I can export a step file it will be very easy to change though as it is a very simple model. You could just shift the four corners of the cutout to where they should be and also the komma.
I have done some more soldering and desoldering of the irf's and sadly I think I got a batch of crapy ones from china, over half of they are partial or completely not working, have to say out of all the parts I ordered from there, this is the worst case of non working parts. Unfortunately the local electronics shop here doesn't have smd components, so I'll add them to my list for next order at mouser or reichelt.

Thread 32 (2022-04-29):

working on pinball data east MPU ?

theck32, 2022-04-29:
I have a data east Mary shelley's Frankenstein pinball and my MPU board is not functional, is it possible to use your board system to make my pinball work? thank you

AmokSolderer, 2022-04-30:
No, you can't use the APC for this DE generation as it doesn't support DMDs.

JustinRudebaugh, 2022-04-30:
Send a message to Chris Hibler http://chrishiblerpinball.com/

Closed 2022-05-02.

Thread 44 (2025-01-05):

MPF Won't Boot Due to Modern Lights Configuration Setting

mythmaker9, 2025-01-05:
MPF is expecting a two byte return from the modern light request.

This is the MPF line in /mpf/platforms/lisy/lisy.py:
`            if self.api_version >= version.parse("0.10"):
                # get number of modern lights
                self.send_byte(LisyDefines.GetModernLightsCount)
                # in api version 10+ this returns two bytes
                self._number_of_modern_lights = await self._read_two_bytes()`

However APC is returning a single byte of 0 to this request causing MPF to lock up waiting for the second byte.  See the code in USBcontrol.ino:
`  case 19:                                            // get number of modern lights
    USB_WriteByte((byte) 0);`

I fixed this simply by adjusting the code to this, however it would be nice if this actually returned the correct value:
`  case 19:                                            // get number of modern lights
    USB_WriteByte((byte) 0);
    USB_WriteByte((byte) 0);`

AmokSolderer, 2025-01-06:
Interesting. I wasn't aware that they changed something there.

However, I guess I just have to implement the same fix as you did as I wouldn't even know what the second byte is supposed to mean. The latest documentation of the Lisy interface (that I'm aware of) still doesn't list it:
https://missionpinball.org/latest/hardware/lisy/protocol/

But zero is probably a good guess because the APC doesn't support MPF's Modern Lights. It can control RGB LEDs, but we figured it would be easier for MPF users to use Facecandy for LEDs which would be directly controlled by the PC.

AmokSolderer, 2025-01-08:
I changed the 1.03 SW accordingly, so the issue should be solved.

Closed 2025-01-08.

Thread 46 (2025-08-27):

Use APC for a complete creation of pinball.

christhell, 2025-08-27:
Hello, first of all thank you so much for this development!
Here I wish to create a fully-fledged pinball machine, an artistic mission.
I bought and partially assembled the APC card. I want to use this card in USB mode with MPF. The MPF environment seems functional on the pc, the DUE card is loaded with "USBcontrol.ino". I haven’t installed a PI or Lisy.
Since I don’t use an existing machine, I have no clue whether APC works or not.
1- Is a Lisy card necessarily necessary to use the USB?
2- How to know if only the APC card works?
3- If I use Lisy in the configuration file for the USB, the card returns that Lisy cannot be reset. (normal not present). But is it normal?
4- Is there a specific configuration in the config file to declare the use of USB? As for the use of Lisy > hardware: USB?
I have so many questions and doubts about this card that doesn’t seem to work, can you enlighten me? I specify that in my project I do not use displays but the PC screen, how to access the configuration menu as can be done with the door button on a real machine?
ps: I was unable to register on the site https://pinside.com/
Thank you immensely, yours sincerely.

MaxPowerTech, 2025-08-29:
Change the initial settings in code.

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

christhell, 2025-08-29:
{"CONNECT TYPE    ",HandleTextSetting,&TxTConType[0][0],0,2} Right?

----- Mail original -----
De: "MaxPowerTech" ***@***.***>
À: "AmokSolderer/APC" ***@***.***>
Cc: "christhell" ***@***.***>, "Author" ***@***.***>
Envoyé: Vendredi 29 Août 2025 16:52:08
Objet: Re: [AmokSolderer/APC] Use APC for a complete creation of pinball. (Issue #46)

MaxPowerTech left a comment (AmokSolderer/APC#46) Change the initial settings in code.

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

—
Reply to this email directly, view it on GitHub , or unsubscribe .
You are receiving this because you authored the thread. Message ID: <AmokSolderer/APC/issues/46/3237309625 @ github . com>

AmokSolderer, 2025-08-30:
Be sure to read the first part of the documentation (Building and setting up an APC) and follow the links where necessary:
https://github.com/AmokSolderer/APC?tab=readme-ov-file#documentation-contents
Especially the sections 1.2 (upload the SW) and 1.5 (run a game) should cover most your questions.

Some additional information:
- For MPF you don't need an SD card and you don't have to change any settings. The default settings are chosen in a way to work with MPF via USB.
- Like MaxPowerTech already wrote, you don't even need an APC board as long as you don't have any pinball HW to control
-  If the connection between MPF and the DUE is successful you should get a corresponding message from MPF

However, I'm not sure that the APC is the best choice for building a completely new machine. It's made for older Williams machines which use a switch matrix, a lamp matrix and segment displays. New machines rather use LEDs, dedicated switches and a TFT monitor and the sound comes from a PC.
Of course you could do this with an APC, but this would be quite an overkill because what you really need is a controller just for solenoids and switches (without a matrix) which can be controlled my MPF.

AmokSolderer, 2025-08-31:
The Arduino DUE has a power LED.
And if problems occur during the programming, the Arduino IDE will complain about a failing upload.

christhell, 2025-08-31:
Yes sure. The Due card seems to be working normally, the LED is well turned on, the upload is done without errors. But no serial feedback in the Arduino console, and no sign on the APC side when powering on/turning on.

No luck because this APC card may be quite ideal for all its I/0 even without a real pinball.

I will try to find the fault.

Thank you again.

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

AmokSolderer, 2025-08-31:
I'd try it without using the serial console as it might get in conflict with MPF's serial connection. And be sure to use the programming port of the DUE.

You can also send serial commands with a terminal program like HTERM.
The APC uses the Lisy protocol for serial communication (that's why you have to select the platform in MPF to Lisy) so if you send a 0 (get connected hardware) it should reply with 'APC':
https://missionpinball.org/latest/hardware/lisy/protocol/#protocol-reference-v008-

christhell, 2025-09-01:
Excellent! Thank you very much for your answers, it helps me a lot.
Indeed I was using the correct programming port, but the serial of Arduino remained active and posed a problem. I was able to test the serial commands with Chataigne (excellent freeware tool) and the APC card responds well and is active. The MFP console replied 'Lisy cannot be reset'.
Thank you
It therefore remains for me to understand why I am unable to see the commands from the APC in MPF. With the PC keyboard, it works. How to perform a simple test to verify this given that I don’t have an HW system? If I use "Input switch number 1" to activate a flipper, is it okay if in the config file I use switch number 1? I don’t quite understand the principle yet.

Chataigne: https://benjamin.kuperberg.fr/chataigne/fr

Closed 2025-08-31.

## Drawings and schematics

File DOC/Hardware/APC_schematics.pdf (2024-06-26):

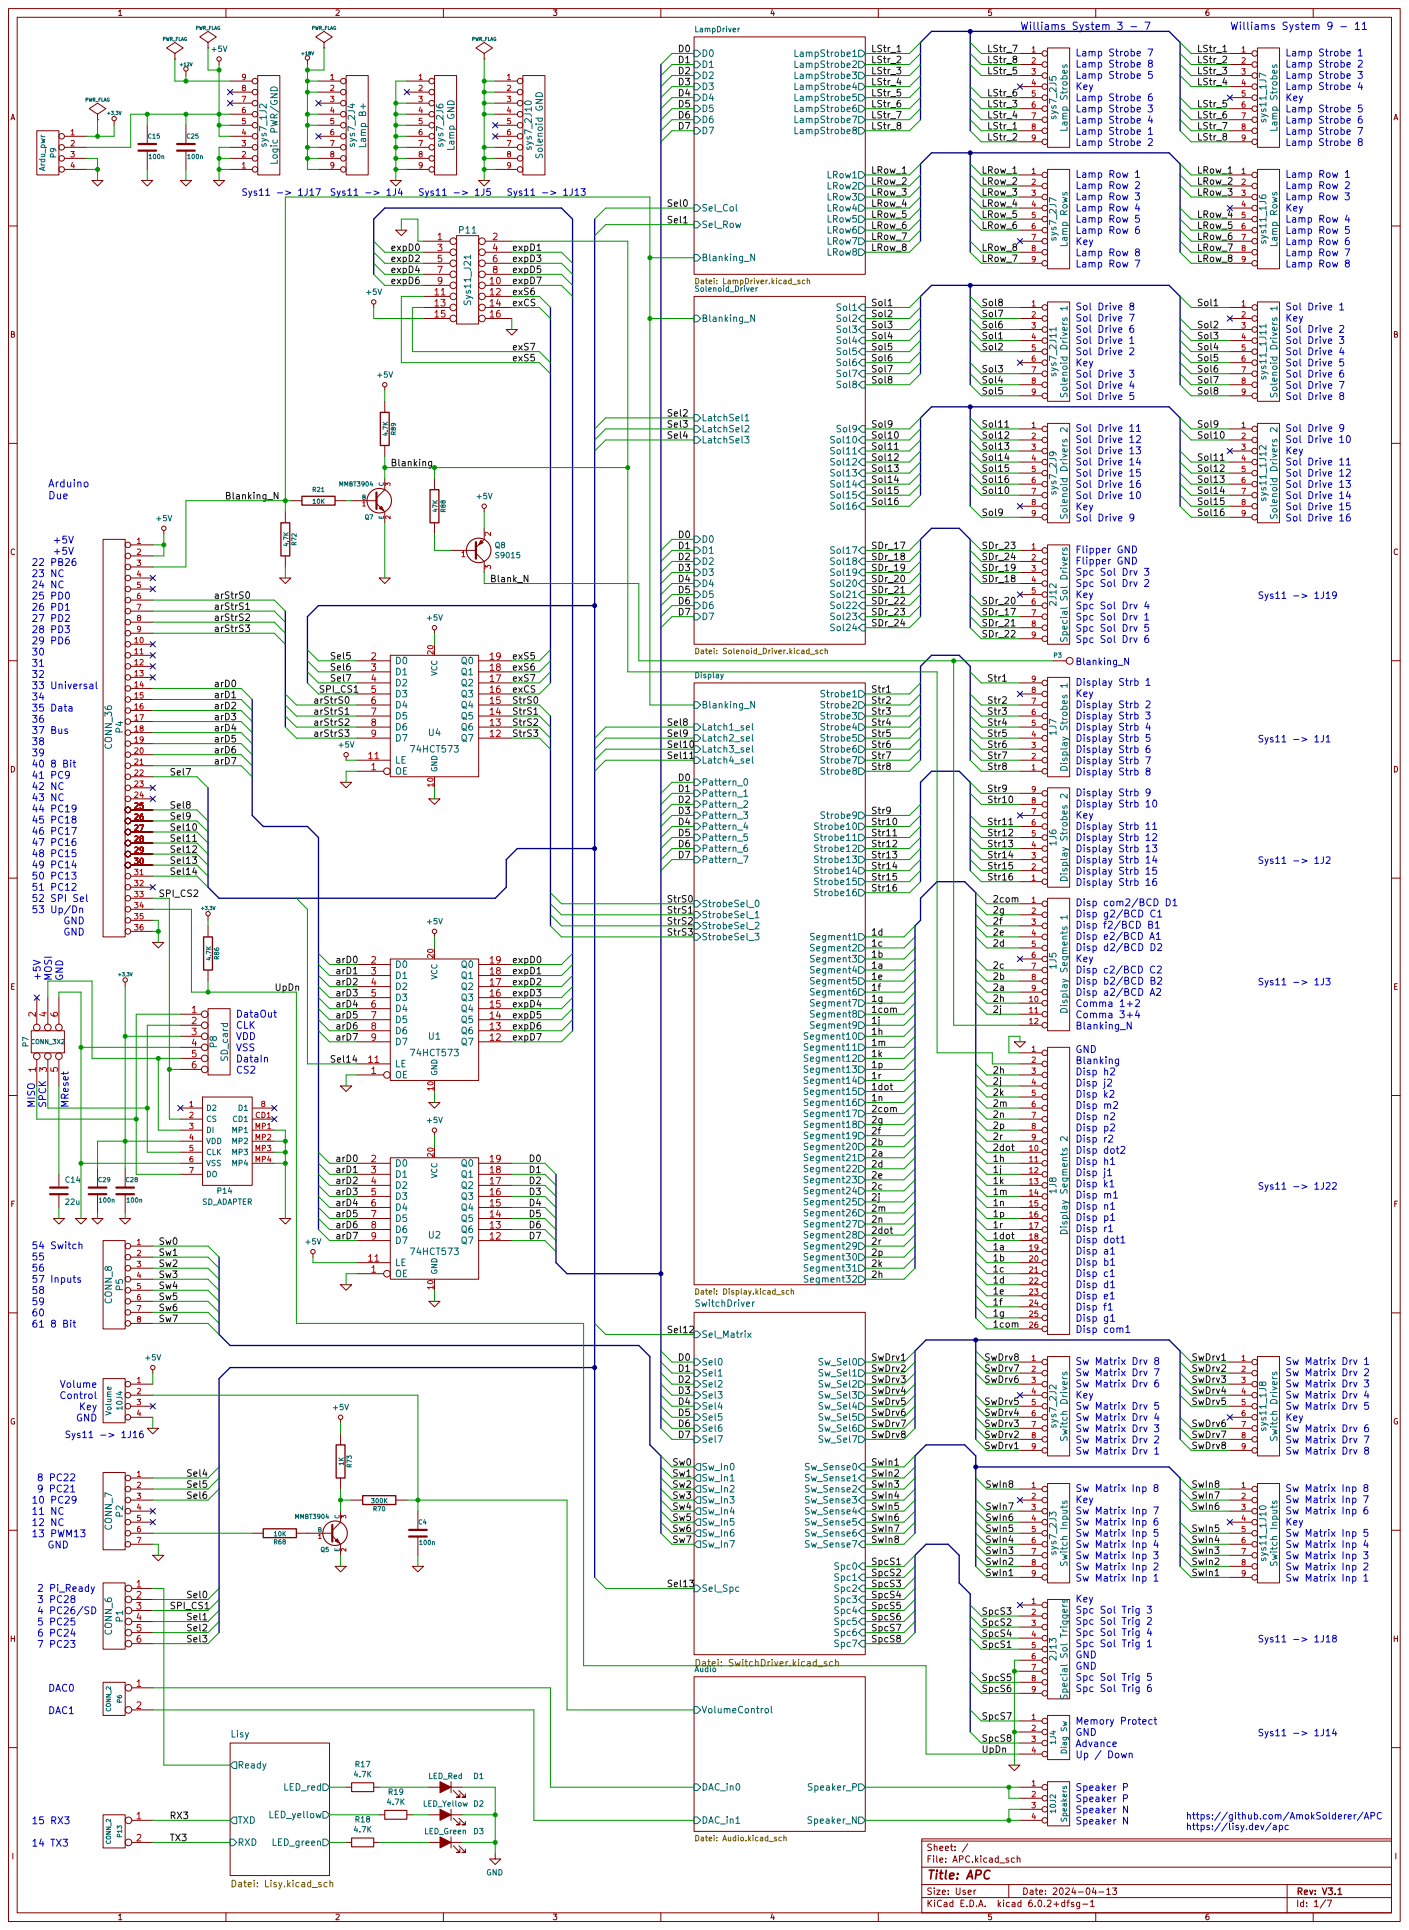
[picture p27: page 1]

https://github.com/AmokSolderer/APC
https://lisy.dev/apc

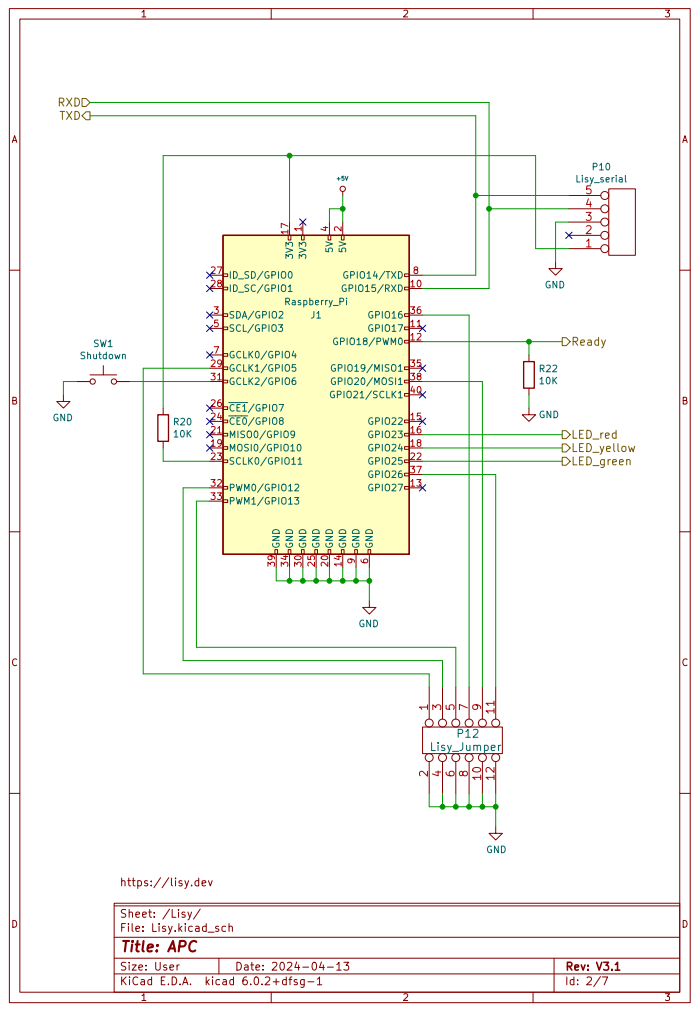
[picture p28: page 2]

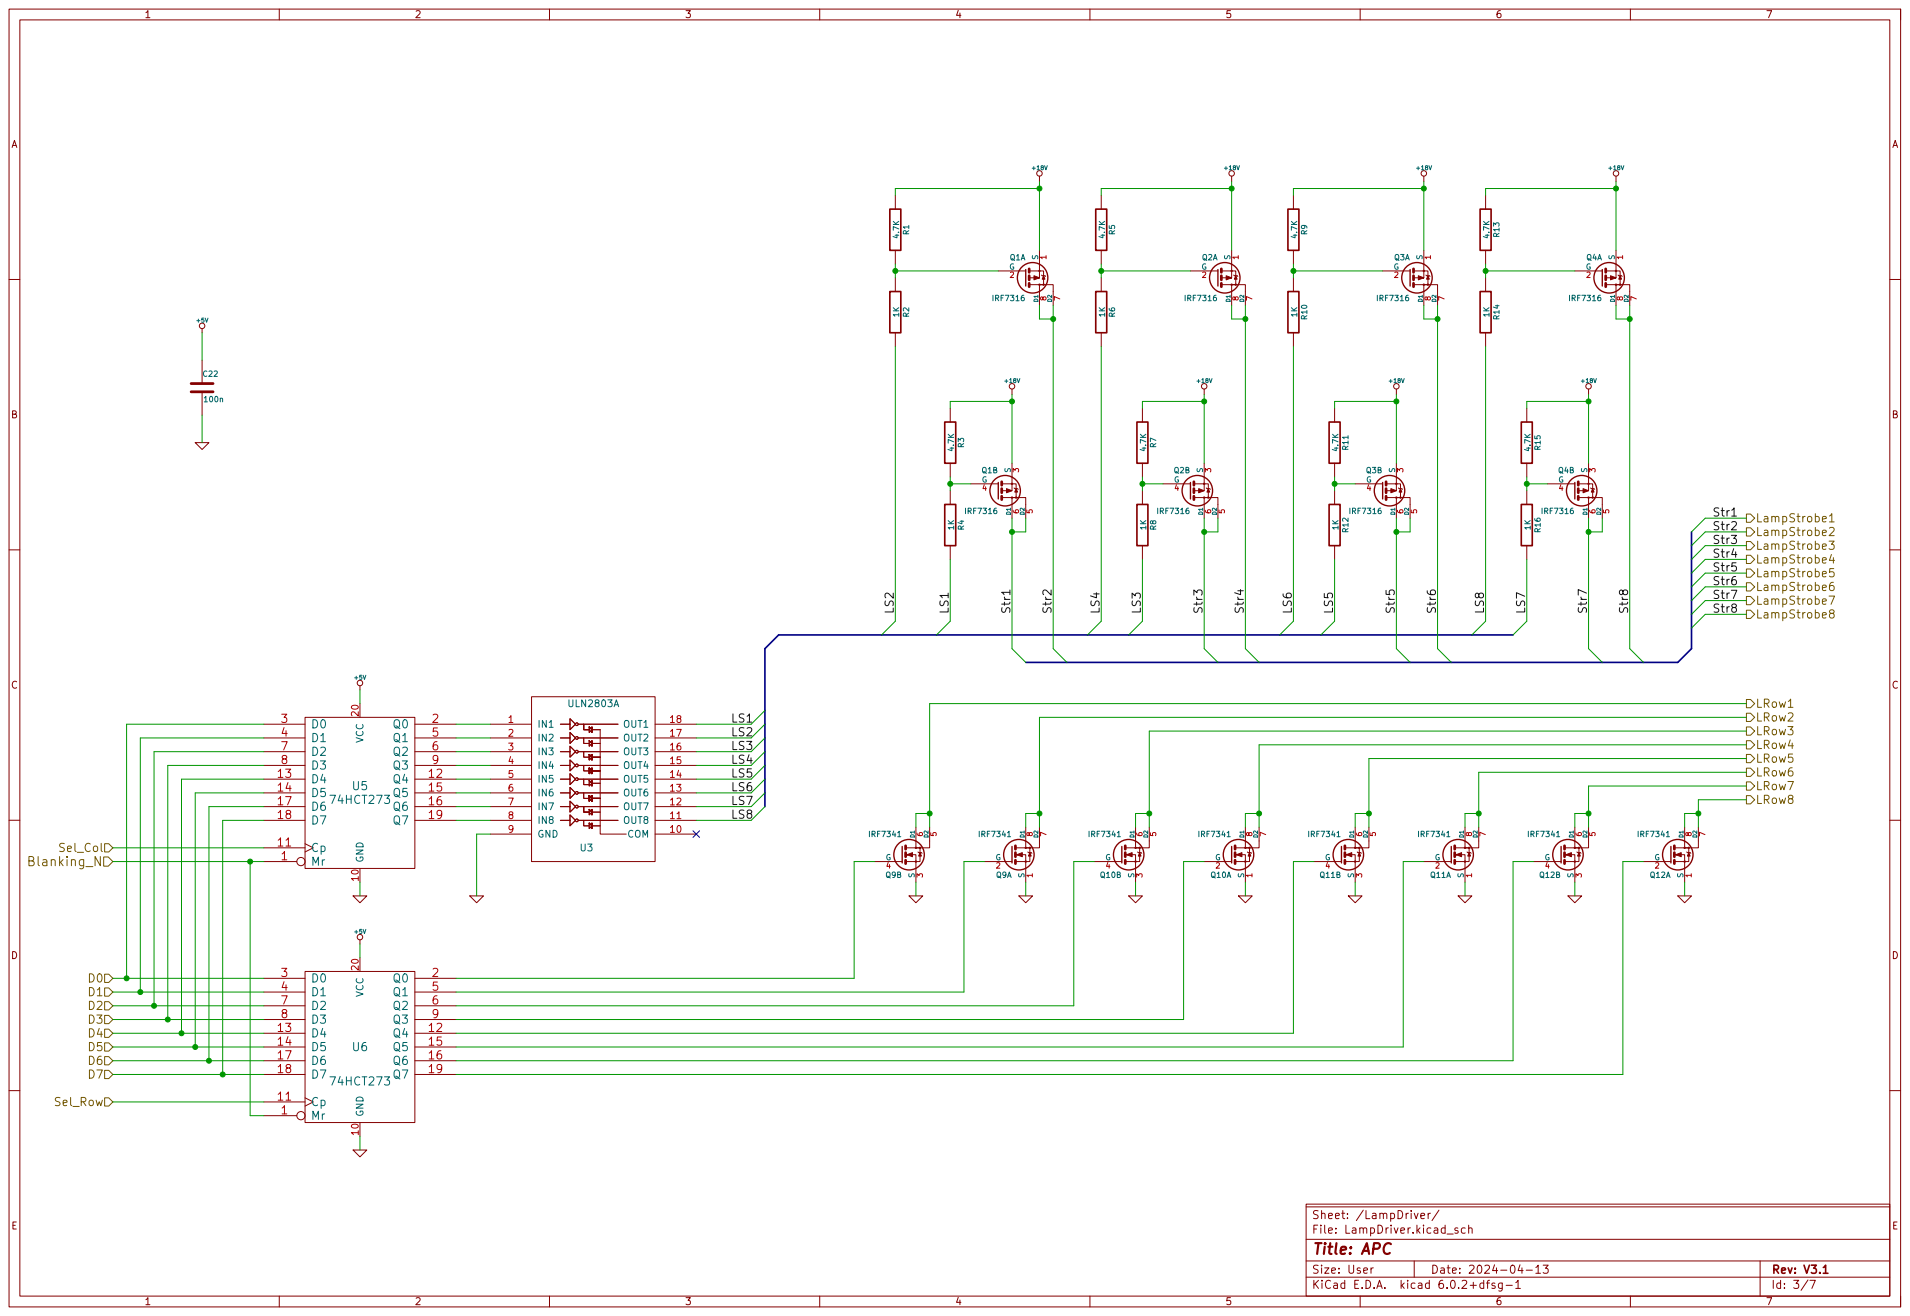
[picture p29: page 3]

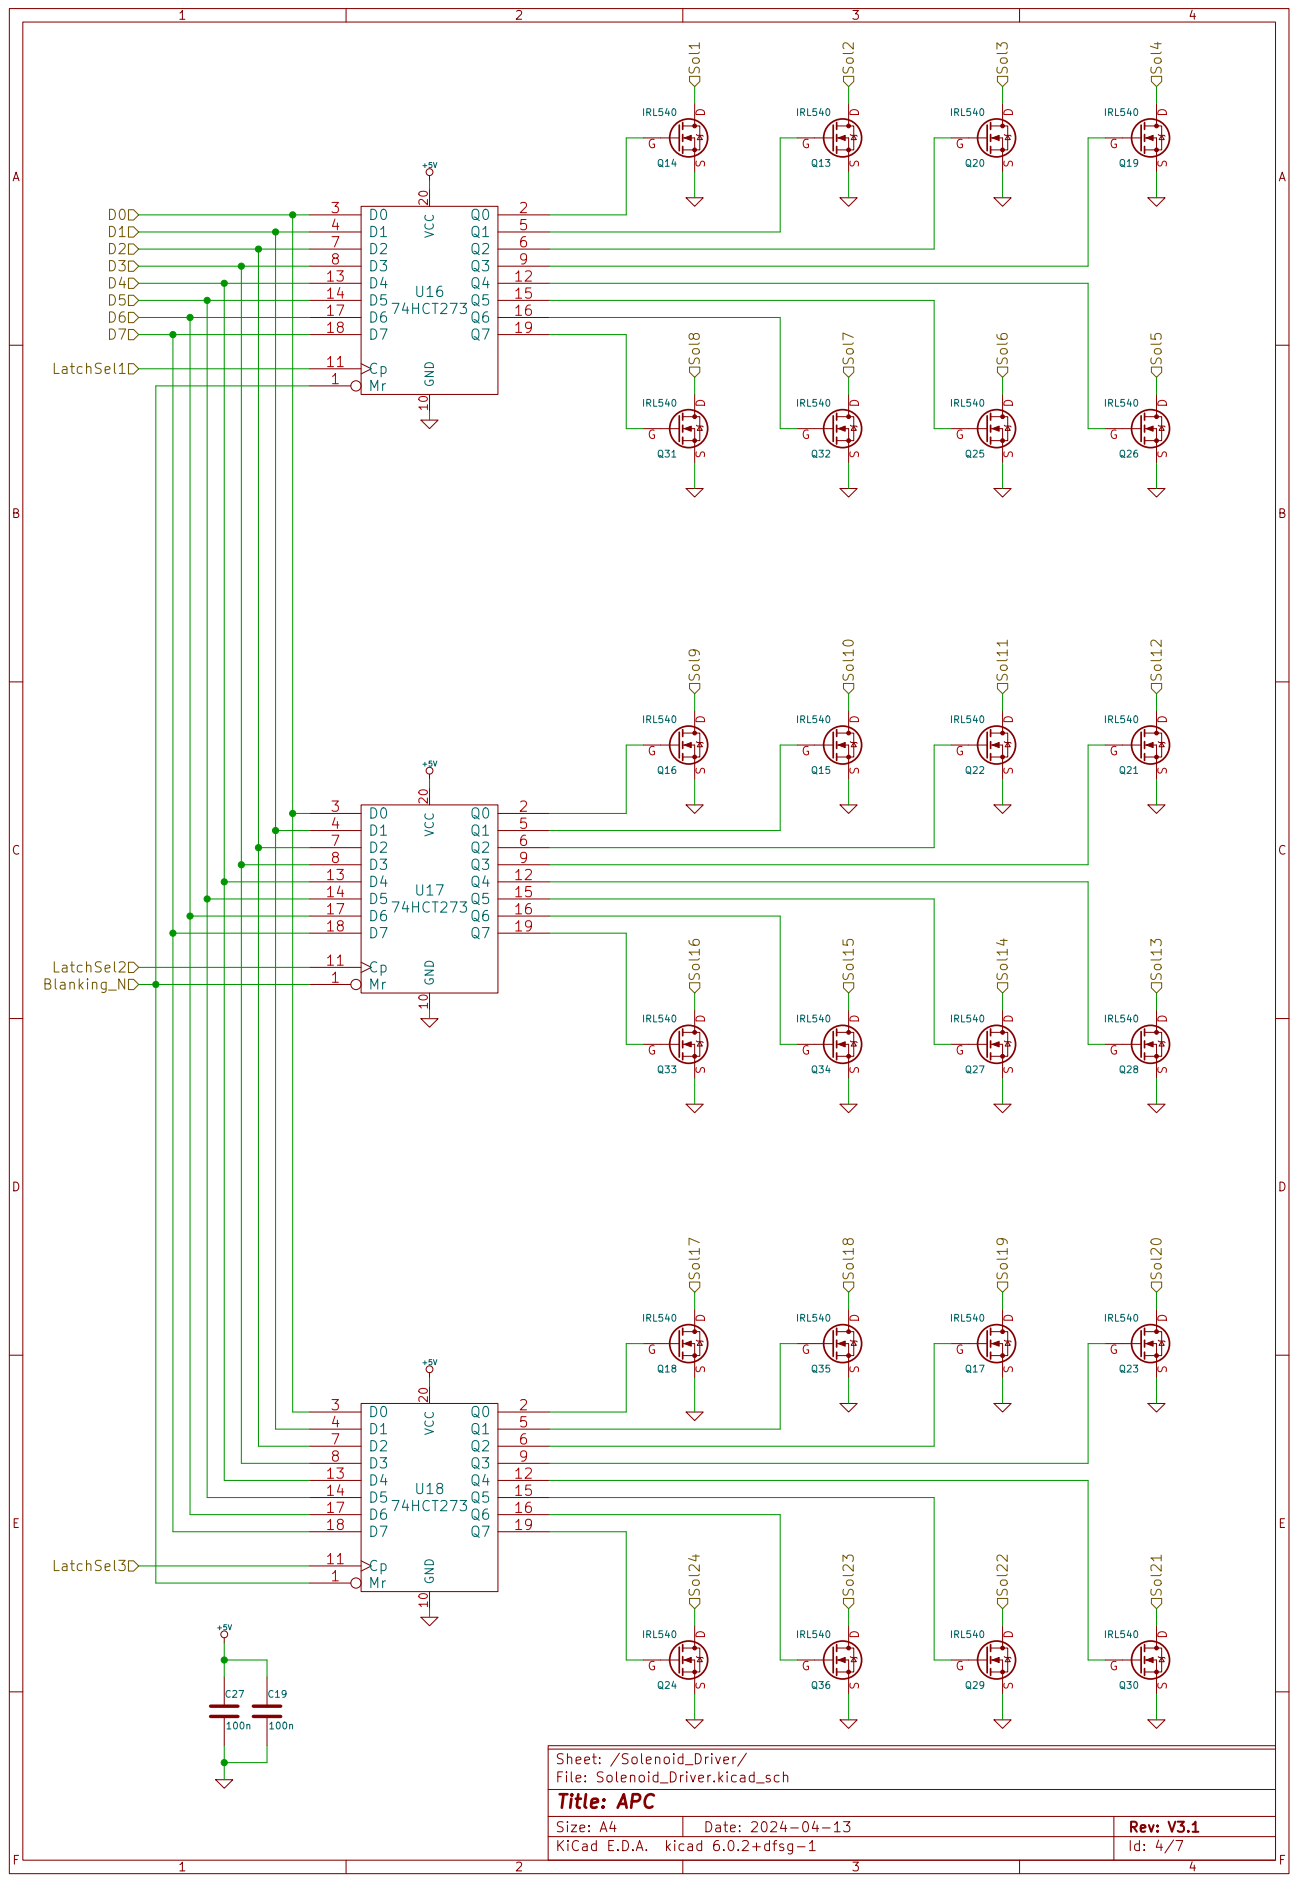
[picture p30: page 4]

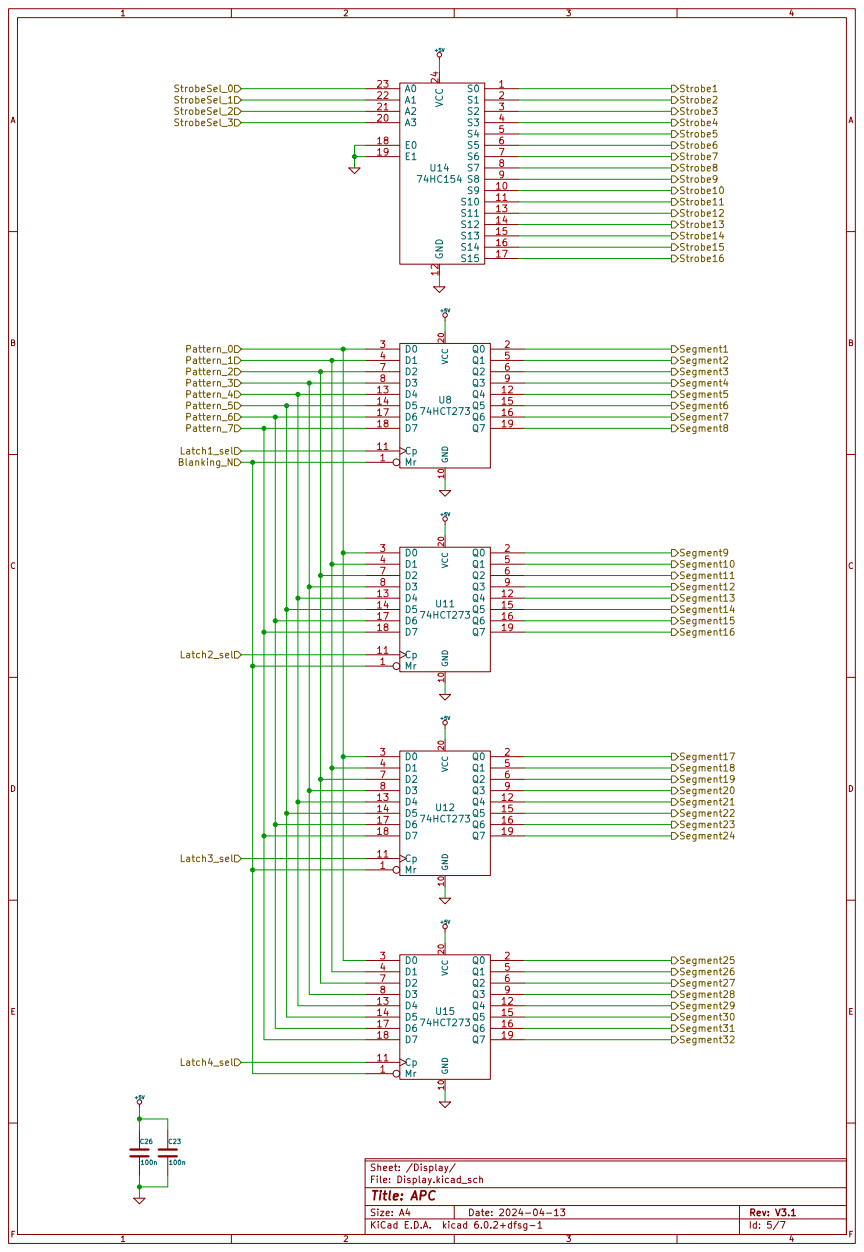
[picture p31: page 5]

Sheet: /Display/ GND 12 VCC 24

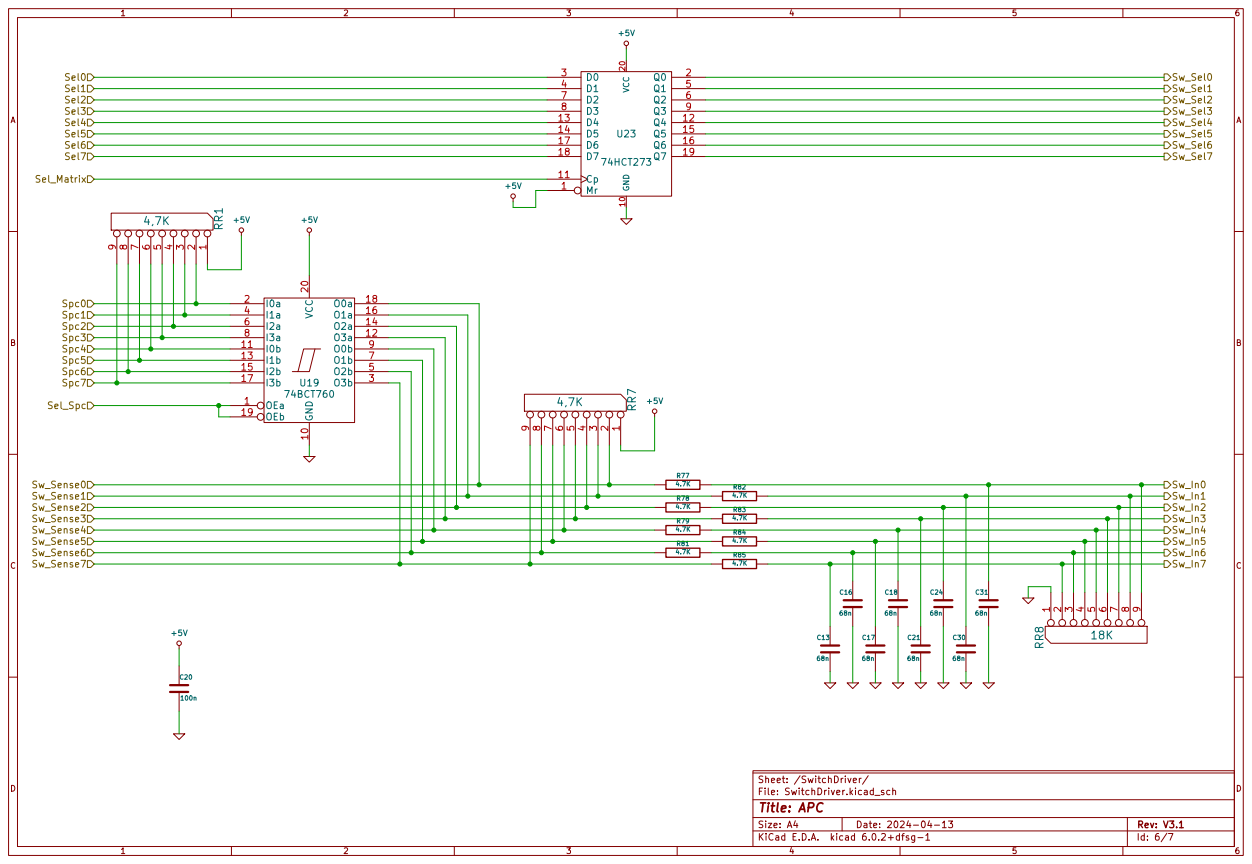
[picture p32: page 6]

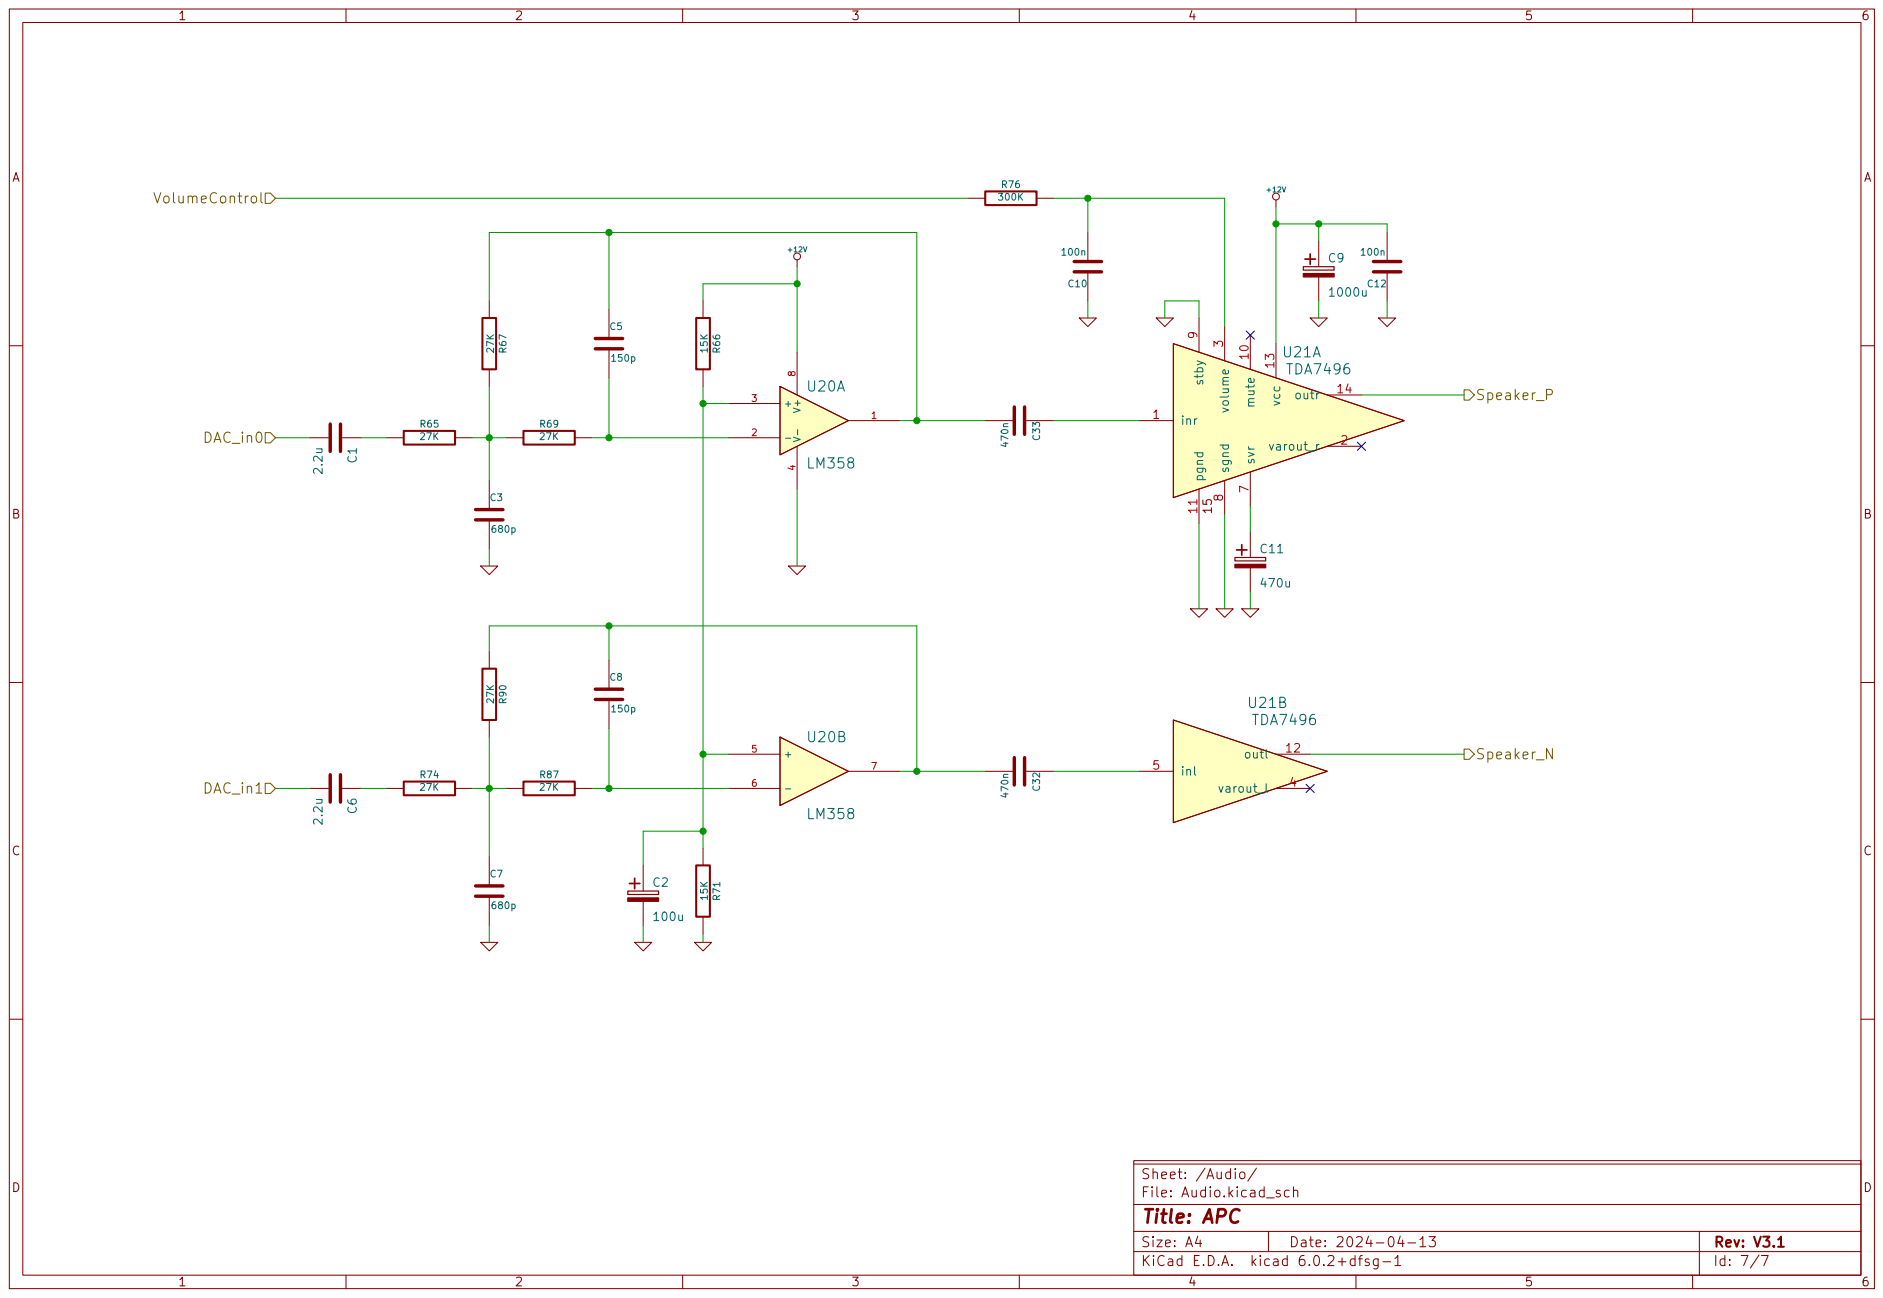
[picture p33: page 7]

File: Audio.kicad_sch Sheet: /Audio/
Id: 7/7 Title: APC

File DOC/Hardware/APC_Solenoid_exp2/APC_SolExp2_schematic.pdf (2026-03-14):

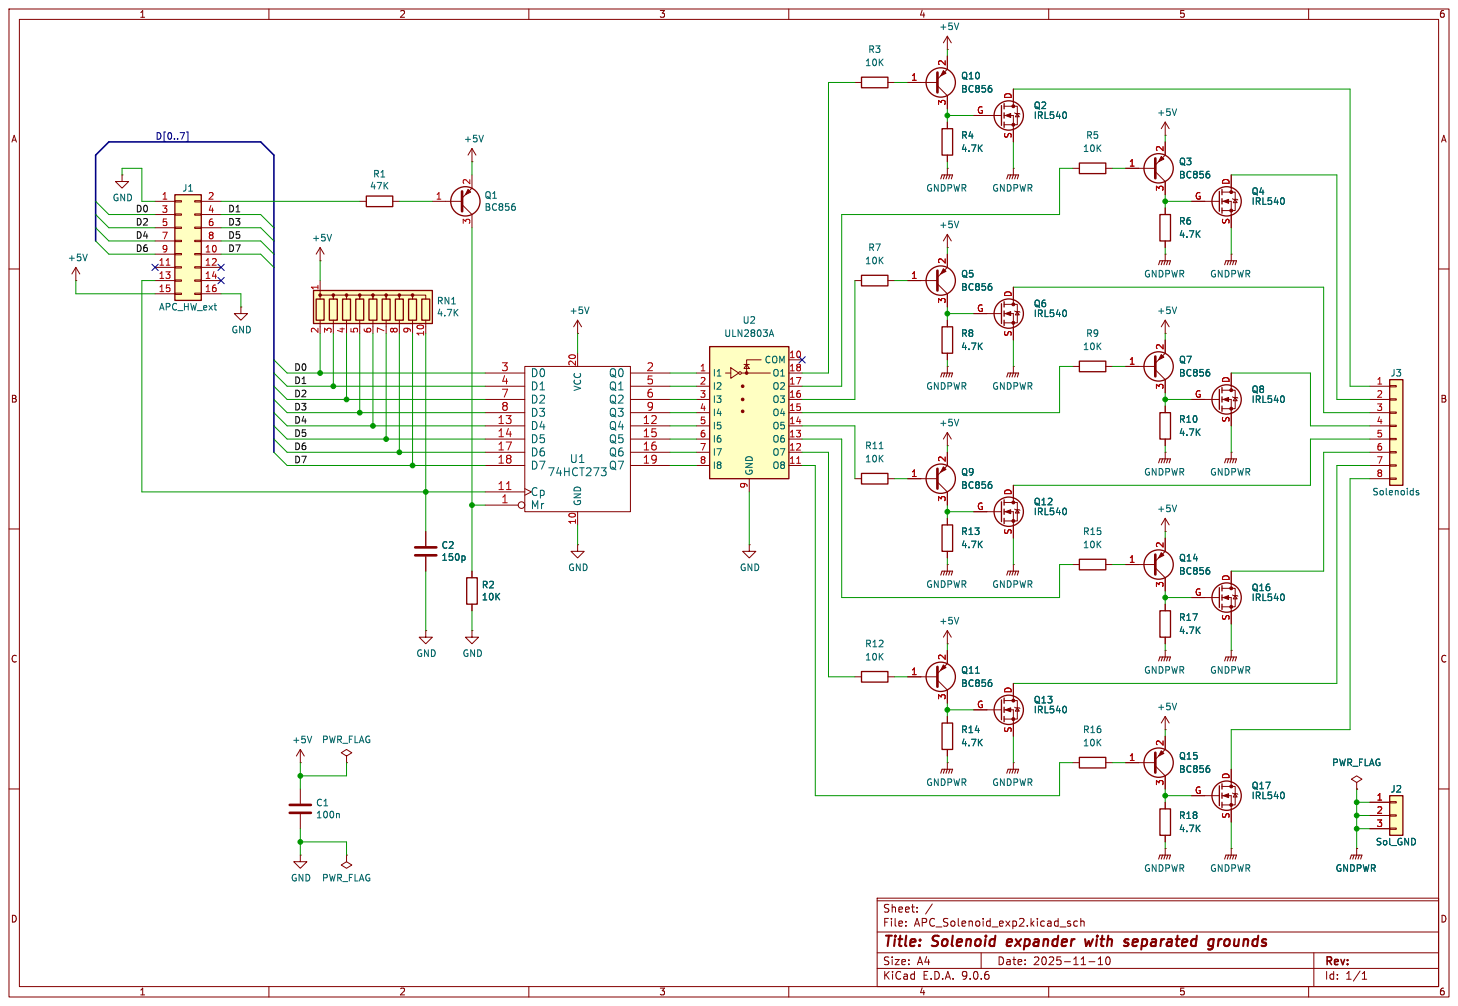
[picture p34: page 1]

Id: 1/1 Title: Solenoid expander with separated grounds

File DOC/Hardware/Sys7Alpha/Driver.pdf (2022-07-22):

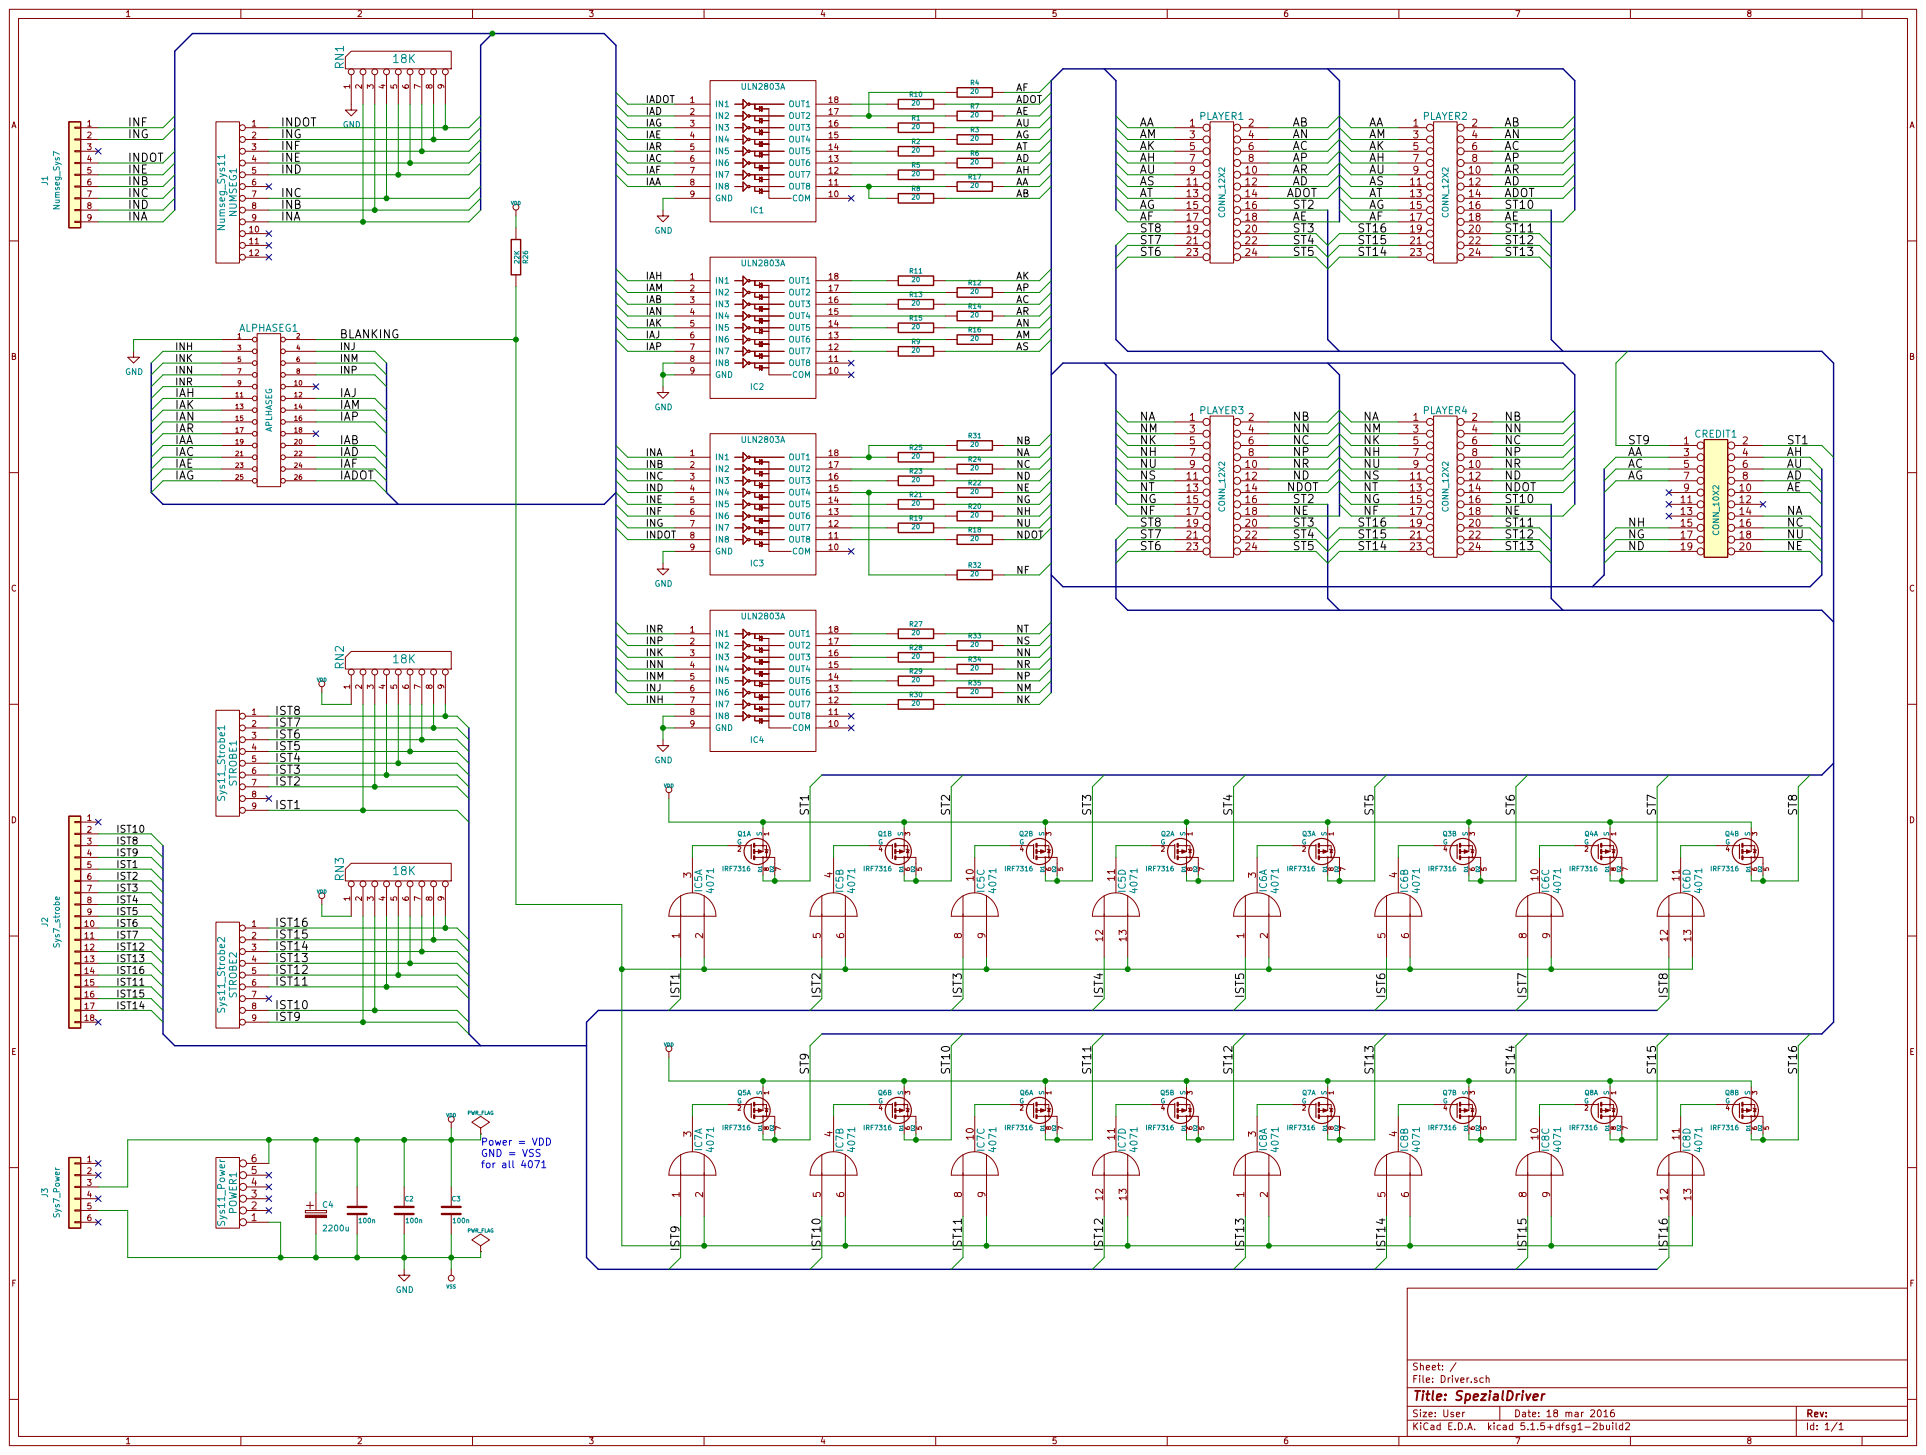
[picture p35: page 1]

ING
INF

INH | INJ
INK | INM

INR | | 10

IAK | 13 | | 14 | IAM
IAN 15 | | | 16

IST8
IST9
IST1
IST2
IST3
IST4
IST5

10 | IST6
11 | IST7
12 | IST12
13 | IST13
14 | IST16
15 | IST11
16 | IST15
17 | IST14

Power = VDD GND = VSS

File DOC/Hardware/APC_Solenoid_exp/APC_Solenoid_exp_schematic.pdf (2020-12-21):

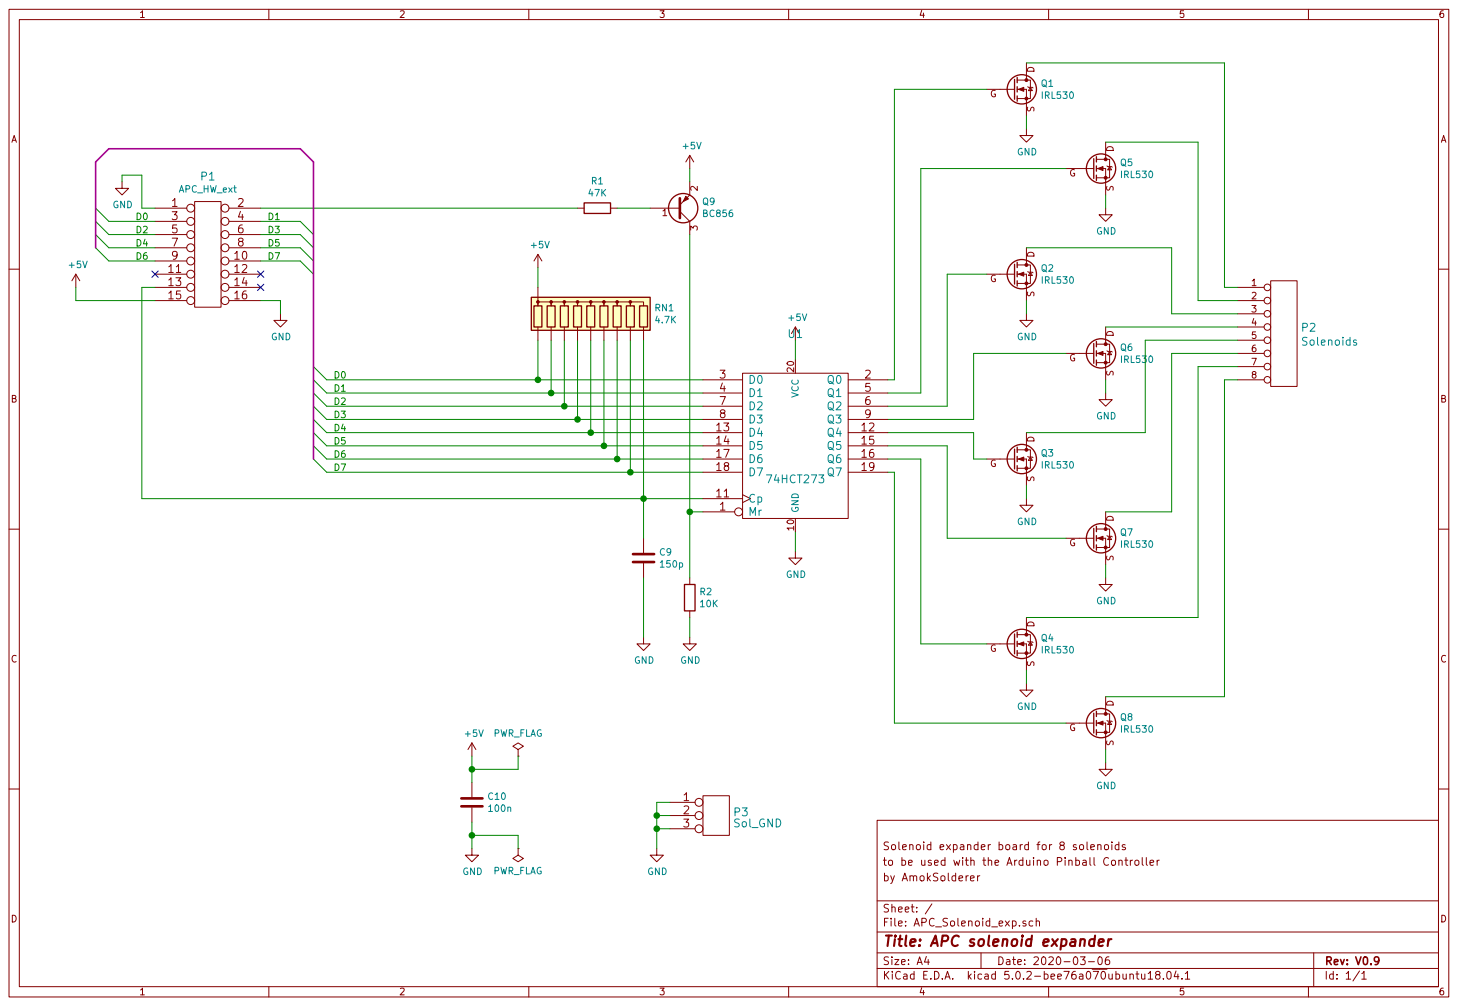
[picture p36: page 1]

File: APC_Solenoid_exp.sch Sheet: / by AmokSolderer

Id: 1/1 Title: APC solenoid expander

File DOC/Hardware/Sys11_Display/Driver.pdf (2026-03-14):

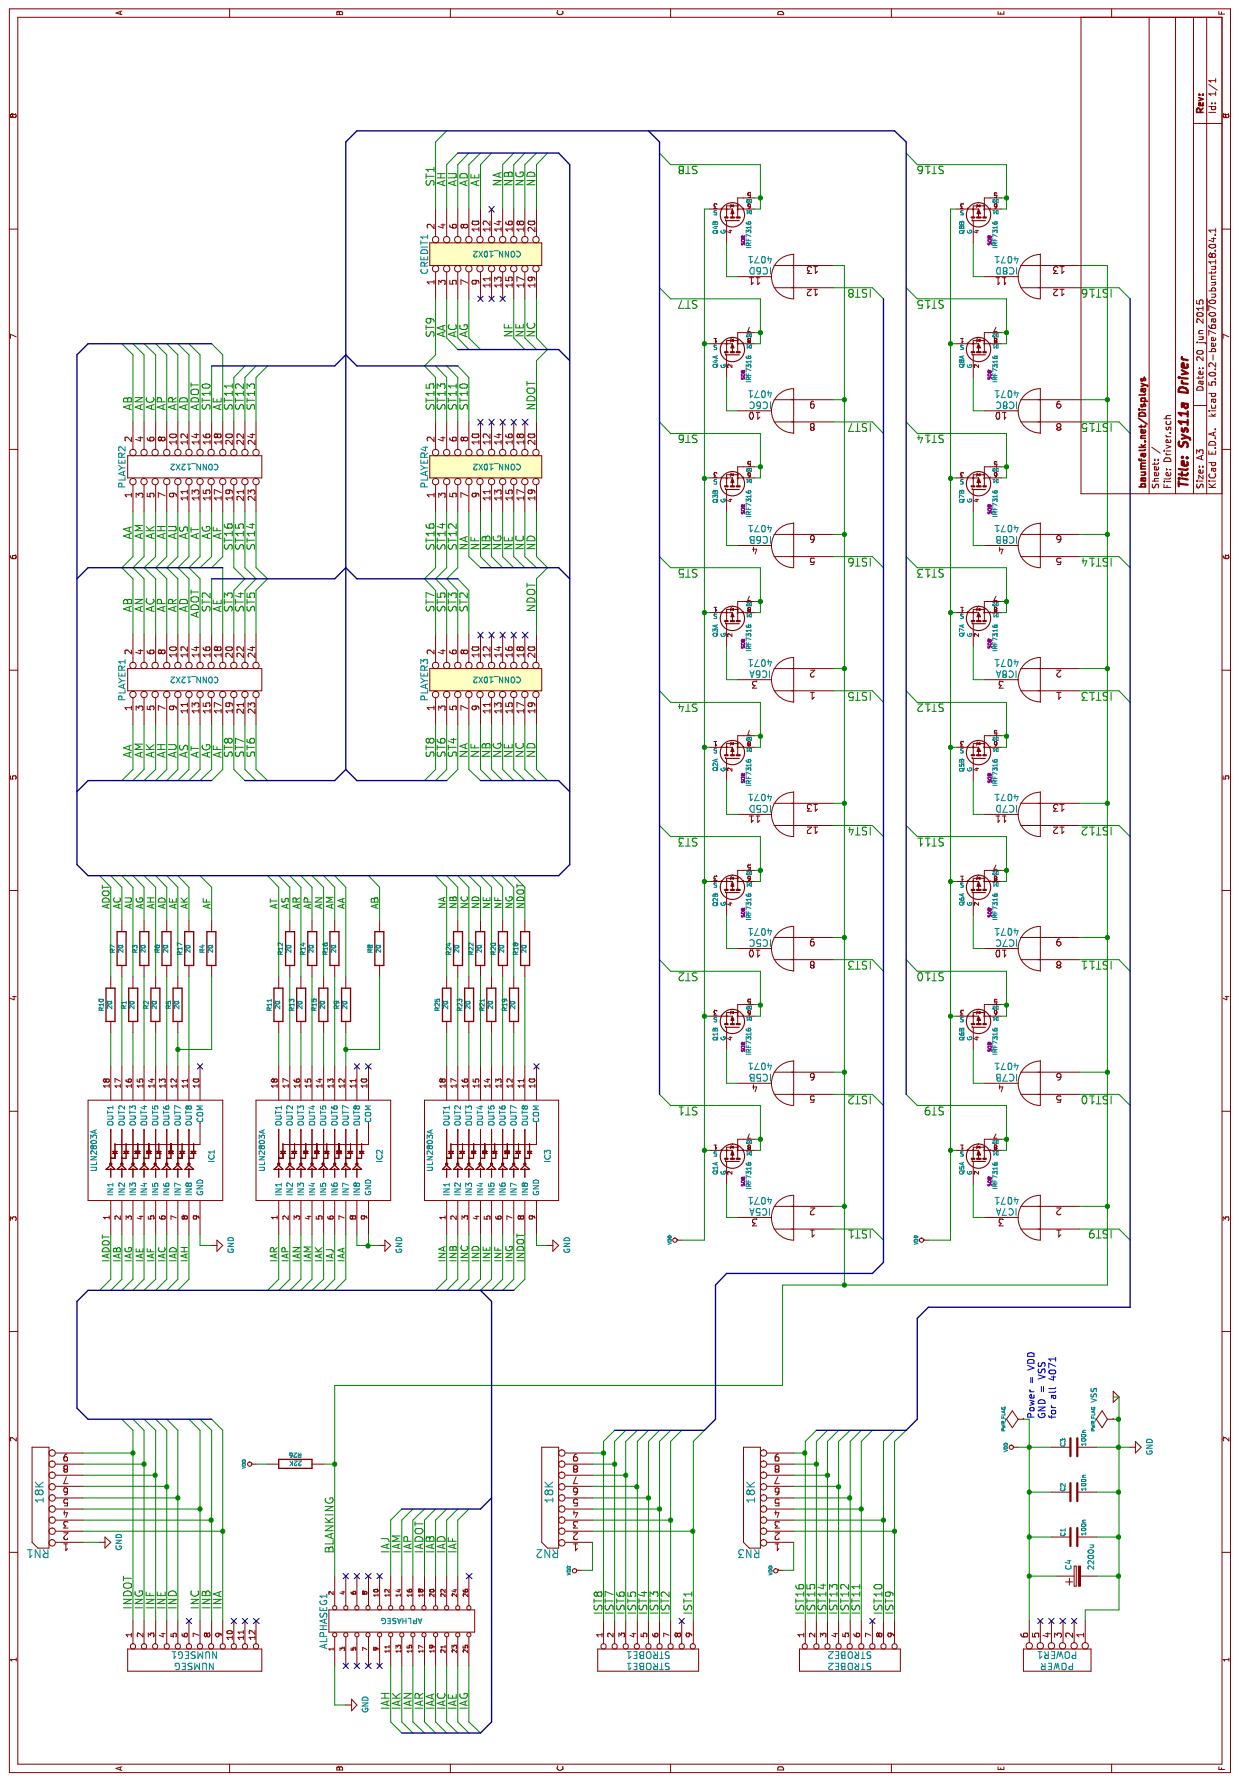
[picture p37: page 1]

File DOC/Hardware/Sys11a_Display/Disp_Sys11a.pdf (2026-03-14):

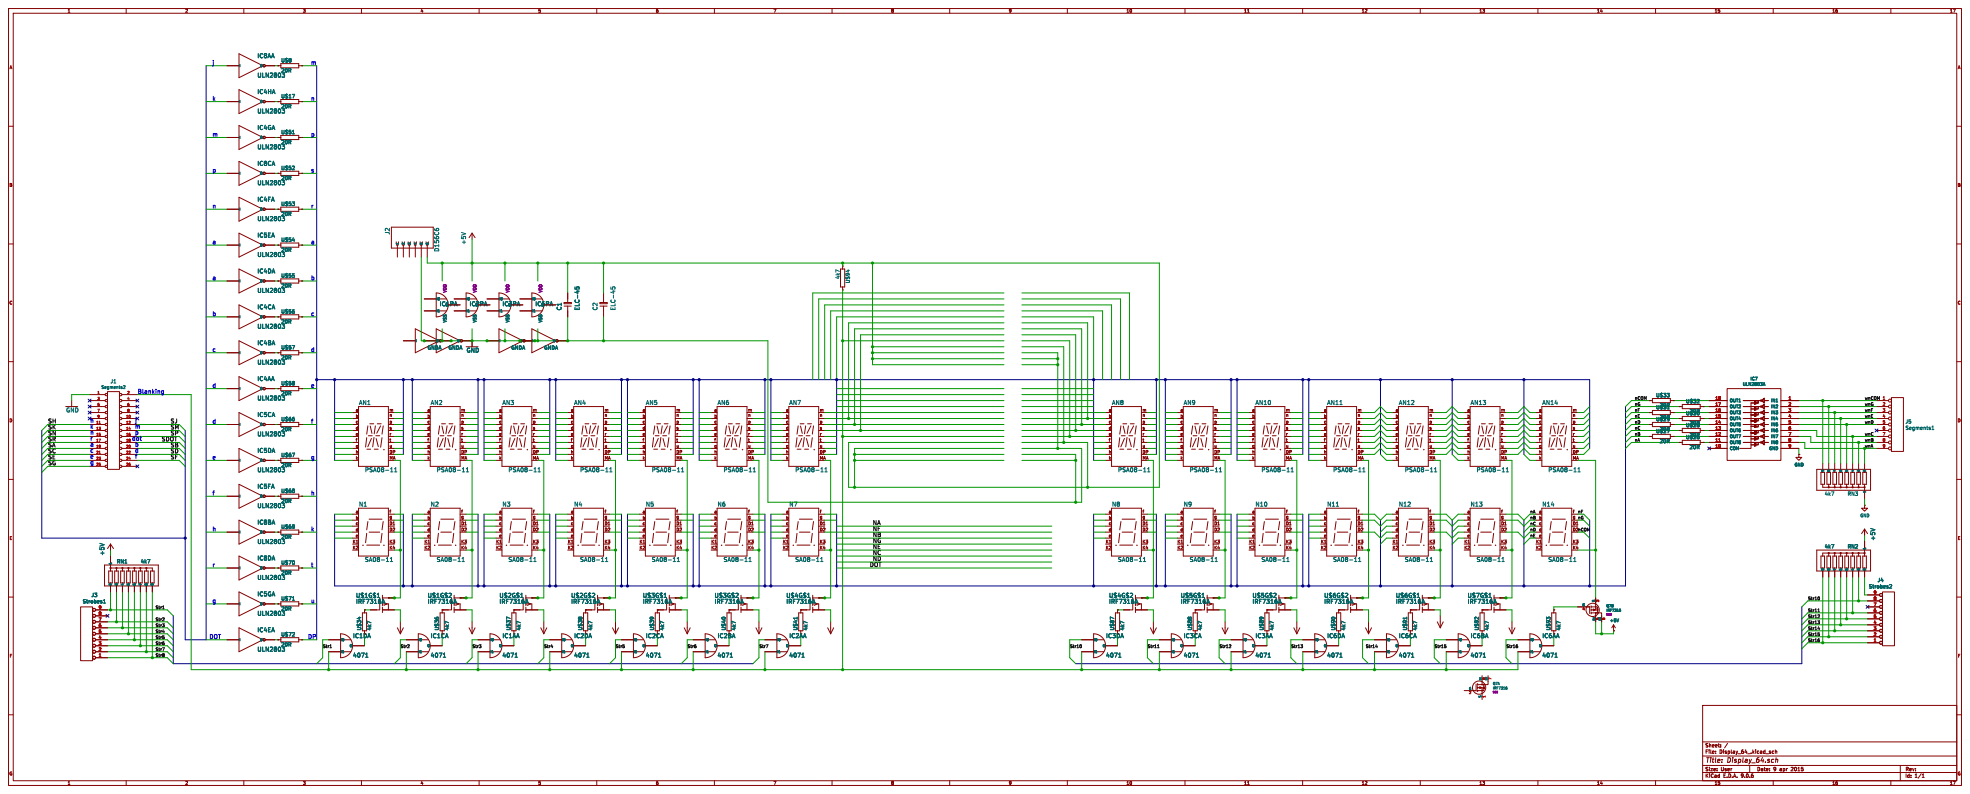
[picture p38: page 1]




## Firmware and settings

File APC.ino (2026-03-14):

#include <SdFat.h>                                    // APC.ino is the operating system for the Arduino Pinball Controller
SdFat SD;
#include <SPI.h>
#include "Arduino.h"
#include "Sound.h"
#define DebugState 0                                  // set this value to 2 for USB debug log
#define UpDown 53                                     // arduino pin connected to the auto/up - manual/Down button
#define Blanking  22                                  // arduino pin to control the blanking signal
#define VolumePin 13                                  // arduino pin to control the sound volume
#define SwMax 72                                      // number of existing switches (max. 72)
#define LampMax 64                                    // number of existing lamps (max. 64)
#define DispColumns 16                                // Number of columns of the used display unit
#define AllSelects 938447360                          // mask for all port C pins belonging to select signals except special switch Sel13 and HW_ext latch select Sel14
#define Sel5 2097152                                  // mask for the Sel5 select signal
#define HwExtSels 606077440                           // mask for all Hw extension port select signals
#define Sel14 8192                                    // mask for the Sel14 select signal
#define Sel13 16384                                   // mask for the Sel13 select signal
#define AllData 510
#define HwExtStackPosMax 20                           // size of the HwExtBuffer

const char APC_Version[6] = "01.04";                  // Current APC version - includes the other INO files also

void HandleBoolSetting(bool change);
void HandleTextSetting(bool change);
void HandleDisplaySetting(bool change);
void HandleNumSetting(bool change);
void HandleVolumeSetting(bool change);
void RestoreDefaults(bool change);
void ExitSettings(bool change);
void watchdogSetup(void){ }

byte (*PinMameException)(byte, byte);

const byte AlphaUpper[128] = {0,0,0,0,0,0,0,0,107,21,0,0,0,0,0,0,0,0,0,0,64,191,64,21,0,0,64,4,0,0,0,40, // Blank $ * + - / for upper row alphanumeric displays
    63,0,6,0,93,4,15,4,102,4,107,4,123,4,14,0,127,4,111,4,0,0,0,0,0,136,65,4,0,34,0,0,0,0, // 0 1 2 3 4 5 6 7 8 9 < = > and fill bytes
    126,4,15,21,57,0,15,17,121,4,120,4,59,4,118,4,0,17,23,0,112,136,49,0,54,10,54,130,63,0, // Pattern A B C D E F G H I J K L M N O
    124,4,63,128,124,132,107,4,8,17,55,0,48,40,54,160,0,170,0,26,9,40,0,0,0,0,0,0,0,0,1,0}; // Pattern P Q R S T U V W X Y Z _

const byte AlphaLower[128] = {0,0,0,0,0,0,0,0,182,35,0,0,0,0,0,0,0,0,0,0,2,247,2,35,0,0,2,2,0,0,0,80, // Blank $ * + - / for lower row alphanumeric displays
    252,0,136,0,122,2,184,2,142,2,182,2,246,2,152,0,254,2,190,2,0,0,0,0,0,68,0,0,0,144,0,0,0,0, // 0 1 2 3 4 5 6 7 8 9 < > and fill bytes
    222,2,184,35,116,0,184,33,118,2,86,2,244,2,206,2,0,33,232,0,70,68,100,0,204,192,204,132,252,0, // Pattern A B C D E F G H I J K L M N O
    94,2,252,4,94,6,182,2,16,33,236,0,68,80,204,20,0,212,0,224,48,80,0,0,0,0,0,0,0,0,32,0}; // Pattern P Q R S T U V W X Y Z _

const byte NumLower[118] = {0,0,0,0,0,0,0,0,0,0,0,0,0,0,0,0,0,0,0,0,0,0,0,0,0,0,0,0,0,0,0,0, // Blank and fill bytes for lower row numeric displays
    252,0,136,0,122,0,186,0,142,0,182,0,246,0,152,0,254,0,190,0,0,0,0,0,70,0,34,0,138,0,184,0,0,0, // 0 1 2 3 4 5 6 7 8 9 = and fill bytes
    222,0,230,0,116,0,234,0,118,0,86,0,246,0,206,0,68,0,232,0,206,0,100,0,194,0,194,0,226,0, // Pattern A B C D E F G H I J K L M N O
    94,0,252,0,66,0,182,0,84,0,236,0,236,0,236,0,206,0,78,0,122,0}; // Pattern P Q R S T U V W X Y Z

const byte LeftCredit[118] = {0,0,0,0,0,0,0,0,0,0,0,0,0,0,0,0,0,0,0,0,0,0,0,0,0,0,0,0,0,0,0,0, // Blank and fill bytes for the left credit (numeric)
    63,0,6,0,93,0,79,0,102,0,107,0,123,0,14,0,127,0,111,0,0,0,0,0,0,0,0,0,0,0,0,0,0,0, // 0 1 2 3 4 5 6 7 8 9 and fill bytes
    0,0,0,0,0,0,0,0,0,0,0,0,0,0,0,0,0,0,0,0,0,0,0,0,0,0,0,0,0,0, // Pattern A B C D E F G H I J K L M N O
    0,0,0,0,0,0,0,0,0,0,0,0,0,0,0,0,0,0,0,0,0,0}; // Pattern P Q R S T U V W X Y Z

const byte RightCredit[118] = {0,0,0,0,0,0,0,0,0,0,0,0,0,0,0,0,0,0,0,0,0,0,0,0,0,0,0,0,0,0,0,0, // Blank and fill bytes for the right credit (numeric)
    252,0,136,0,122,0,186,0,142,0,182,0,246,0,152,0,254,0,190,0,0,0,0,0,0,0,0,0,0,0,0,0,0,0, // 0 1 2 3 4 5 6 7 8 9 and fill bytes
    0,0,0,0,0,0,0,0,0,0,0,0,0,0,0,0,0,0,0,0,0,0,0,0,0,0,0,0,0,0, // Pattern A B C D E F G H I J K L M N O
    0,0,0,0,0,0,0,0,0,0,0,0,0,0,0,0,0,0,0,0,0,0}; // Pattern P Q R S T U V W X Y Z

const int LampPeriod = 2;                             // Lamp cycle period in ms
const byte NoLamps[8] = {0,0,0,0,0,0,0,0};
const byte AllLamps[8] = {255,255,255,255,255,255,255,255};

// system variables

unsigned int IntBuffer;                               // general purpose buffer
byte ByteBuffer = 0;                                  // general purpose buffer
byte ByteBuffer2 = 0;                                 // general purpose buffer
byte IRQerror = 0;                                    // general purpose counter
bool SDfound = false;                                 // SD card present?
volatile byte SwitchStack = 0;                        // determines which switch events stack is active
byte ChangedSw[2][30];                                // two stacks of switches with pending events
byte SwEvents[2];                                     // contains the number of pending switch events in each stack
uint32_t SwitchRows[10] = {29425756,29425756,29425756,29425756,29425756,29425756,29425756,29425756,29425756,29425756};// stores the status of all switch rows
const byte *DispRow1;                                 // determines which patterns are to be shown (2 lines with 16 chars each)
const byte *DispRow2;
const byte *DispPattern1;                             // points to the correct character patterns for this kind of display
const byte *DispPattern2;
byte DisplayUpper[32];                                // changeable display buffer
byte DisplayLower[32];
byte DisplayUpper2[32];                               // second changeable display buffer
byte DisplayLower2[32];
const uint16_t *LEDpatDuration;                       // sets the time until the next LED pattern is shown
const byte *LEDpattern;                               // determines which LED pattern is to be shown (only active with 'LED lamps' = 'Additional' and depends on the 'No of LEDs' setting)
const byte *LEDpointer;                               // Pointer to the LED flow to be shown
void (*LEDreturn)(byte);                              // Pointer to the procedure to be executed after the LED flow has been shown
const byte *LampPattern;                              // determines which lamp pattern is to be shown (depends on the 'Backbox Lamps' setting)
const byte *LampBuffer;
byte LampColumns[8];                                  // stores the status of all lamp columns
bool StrobeLightsOn;                                  // Indicates that the playfield lamps are strobing
const struct LampPat *PatPointer;                     // Pointer to the lamp flow to be shown
struct LampPat {                                      // a lamp pattern sequence played by ShowLampPatterns
  uint16_t Duration;
  byte Pattern[8];};
struct LampFlow {                                     // defines a series of lamp patterns shown by AttractLampCycle
  uint16_t Repeat;
  const struct LampPat *FlowPat;};
short FlowRepeat = 0;                                 // number of repeats for the LampFlow
void (*LampReturn)(byte);                             // Pointer to the procedure to be executed after the lamp flow has been shown
byte BlinkTimers = 0;                                 // number of active blink timers
byte BlinkTimer[65];                                  // timer used for blinking lamps
byte BlinkingNo[65];                                  // number of lamps using this BlinkTimer
unsigned int BlinkPeriod[65];                         // blink period for this timer
byte BlinkingLamps[65][65];                           // [BlinkTimer] used by these [lamps]
byte SolMax = 24;                                     // maximum number of solenoids
volatile bool SolChange = false;                      // Indicates that the state of a solenoid has to be changed
byte SolRecycleTime[22];                              // recycle time for each solenoid
byte SolRecycleTimers[22];                            // stores the numbers of the recycle timers for each solenoid
bool C_BankActive = false;                            // A/C relay currently doing C bank?
byte SolWaiting[256][2];                              // list of waiting A/C solenoid requests
byte ACselectRelay = 0;                               // solenoid number of the A/C select relay
byte ActSolSlot = 0;                                  // currently processed slot in SolWaiting
byte NextSolSlot = 0;                                 // next free slot in SolWaiting
byte SettingsRepeatTimer = 0;                         // number of the timer of the key repeat function in the settings function
byte BallWatchdogTimer = 0;                           // number of the ball watchdog timer
byte CheckReleaseTimer = 0;                           // number of the timer for the ball release check
volatile bool BlockPrioTimers = false;                // blocks the prio timer interrupt while timer properties are being changed
byte ActivePrioTimers = 0;                            // Number of active prio timers
unsigned int PrioTimerValue[9];                       // Timer value
byte PrioTimerArgument[9];
void (*PrioTimerEvent[9])(byte);                      // pointers to the procedures to be executed on the prio timer event
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
void loop() {
  byte c = 0;                                         // initialize counter
  byte i = 0;
  if (IRQerror) {
    ErrorHandler(IRQerror,0,0);
    IRQerror = 0;}
  if (SwEvents[SwitchStack]) {                        // switch event pending?
    byte SwitchBuffer = SwitchStack;
    if (SwitchBuffer) {                               // switch to the other stack to avoid a conflict with the interrupt
      SwitchStack = 0;}
    else {
      SwitchStack = 1;}
    while (SwEvents[SwitchBuffer]) {                  // as long as there are switch events to process
      if (ChangedSw[SwitchBuffer][c]) {               // pending switch event found?
        SwEvents[SwitchBuffer]--;                     // decrease number of pending events
        i = ChangedSw[SwitchBuffer][c];               // buffer the switch number
        ChangedSw[SwitchBuffer][c] = 0;               // clear the event
        if (QuerySwitch(i)) {                         // process SET switches
          Switch_Pressed(i);}                         // access the set switch handler
        else {                                        // process released switches
          Switch_Released(i);}}                       // access the released switch handler
      if (c < 29) {                                   // number of pending events still in the allowed range?
        c++;}                                         // increase counter
      else {
        ErrorHandler(21,0,c);}}}
  c = 0;                                              // initialize counter
  if (TimerEvents[TimerStack]) {                      // timer event pending?
    byte StackBuffer = TimerStack;
    if (StackBuffer) {                                // switch to the other stack to avoid a conflict with the interrupt
      TimerStack = 0;}
    else {
      TimerStack = 1;}
    while (TimerEvents[StackBuffer]) {                // as long as there are timer events to process
      if (RunOutTimers[StackBuffer][c]) {             // number of run out timer found?
        TimerEvents[StackBuffer]--;                   // decrease number of pending events
        i = RunOutTimers[StackBuffer][c];             // buffer the timer number
        void (*TimerBuffer)(byte) = TimerEvent[i];    // Buffer the event for this timer
        if (!TimerBuffer) {                           // TimerEvent must be specified
          ErrorHandler(20,0,c);}
        RunOutTimers[StackBuffer][c] = 0;             // delete the timer from the list
        TimerEvent[i] = 0;                            // delete the event to show the timer as free
        TimerBuffer(TimerArgument[i]);}               // call event procedure
      if (c < 29) {                                   // number of pending events still in the allowed range?
        c++;}                                         // increase counter
      else {
        ErrorHandler(22,0,c);}}}                      // increase search counter
  if (SoundPrio) {                                    // which channel has to be processed first?
    if (!StopSound && (SBP != SoundIRpos)) {          // still sound data to read?
      ReadSound();}                                   // read it
    else {                                            // no sound data?
      if (AfterSoundPending == 1) {                   // is there an after sound event pending?
        AfterSoundPending = 0;                        // reset the flag
        if (AfterSound) {                             // really?
          AfterSound(0);}}                            // call it
      else {                                          // no after sound event
        if (!StopMusic && (MBP != MusicIRpos)) {      // proceed with music
          ReadMusic();}
        else {                                        // no music data?
          if (AfterMusicPending == 1) {               // is there an after music event pending?
            AfterMusicPending = 0;                    // reset the flag
            if (AfterMusic) {                         // really?
              AfterMusic(0);}}}}}}                    // call it
  else {                                              // same as above but with the priority on music
    if (!StopMusic && (MBP != MusicIRpos)) {
      ReadMusic();}
    else {
      if (AfterMusicPending == 1) {
        AfterMusicPending = 0;
        if (AfterMusic) {
          AfterMusic(0);}}
      else {
        if (!StopSound && (SBP != SoundIRpos)) {
          ReadSound();}
        else {
          if (AfterSoundPending == 1) {
            AfterSoundPending = 0;
            if (AfterSound) {
              AfterSound(0);}}}}}}
  if (ComState) {                                     // Remote mode?
    if (ComState == 1) {                              // onboard Pi selected?
      if (!OnBoardCom && (REG_PIOB_PDSR & 33554432)) {  // onboard com off and Pi detected?
        Serial3.begin(115200);                        // needed for onboard serial communication
        OnBoardCom = true;}}
    if(USB_Available()) {
      USB_SerialCommand();}}}                         // use the first received byte as a command

void ReadMusic() {                                    // read music data from SD
  if (MusicFile.available() > 255) {                  // enough data remaining in file to fill one block?
    MusicFile.read(MusicBuffer+MBP*128,2*128);        // read one block
    MBP++;                                            // increase read pointer
    if (MBP == 16) {                                  // last block reached?
      MBP = 0;                                        // start over
      if (!PlayingMusic) {                            // not already playing?
        PlayingMusic = true;                          // start playing
        StartMusic = false;}}}                        // stop init phase
  else {                                              // not enough data to fill one block
    byte Avail = MusicFile.available();               // determine how much is left
    MusicFile.read(MusicBuffer+MBP*128,Avail);        // read it
    for (byte i=0; i<128-Avail/2; i++) {                   // fill the rest with silence
      *(MusicBuffer+MBP*128+Avail/2+i) = 2048;}
    MBP++;                                            // increase read pointer
    if (MBP == 16) {                                  // last block read?
      MBP = 0;}                                       // start over
    StopMusic = MBP;                                  // mark this block as being the last
    MusicFile.close();}                               // close file
  SoundPrio = true;}                                  // switch priority to sound

void ReadSound() {                                    // same as above but for the sound channel
  if (SoundFile.available() > 255) {
    SoundFile.read(SoundBuffer+SBP*128,2*128);
    SBP++;
    if (SBP == 16) {
      SBP = 0;
      if (!PlayingSound) {
        PlayingSound = true;
        StartSound = false;}}}
  else {
    byte Avail = SoundFile.available();
    SoundFile.read(SoundBuffer+SBP*128,Avail);
    for (byte i=0; i<128-Avail/2; i++) {
      *(SoundBuffer+SBP*128+Avail/2+i) = 2048;}
    SBP++;
    if (SBP == 16) {
      SBP = 0;}
    StopSound = SBP;
    SoundFile.close();}
  SoundPrio = false;}
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

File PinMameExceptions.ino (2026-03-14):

#define SoundCommandCh1 0
#define SoundCommandCh2 1
#define SwitchActCommand 2
#define SwitchRelCommand 3
#define SolenoidActCommand 4
#define SolenoidRelCommand 5
#define LampOnCommand 6
#define LampOffCommand 7
#define WriteToDisplay0 8
#define WriteToDisplay1 9
#define WriteToDisplay2 10
#define WriteToDisplay3 11
#define WriteToDisplay4 12

#define USB_BallSave 5                                // optional ball saver
#define USB_BallSaveTime 6                            // activation time for the optional ball saver
#define USB_BGmusic 7                                 // to select an own BG music

#define SwOuthole 0                                   // number of the outhole switch
#define SwTrunk1 1                                    // number of the 1st trunk switch (active if one ball is in the trunk) - set to 0 if machine has only one ball (-> no trunk)
#define SwTrunk2 2                                    // number of the 2nd trunk switch (active if a second ball is in the trunk)
#define SwTrunk3 3                                    // number of the 3rd trunk switch (active if a third ball is in the trunk) - set to 0 if machine has only two balls
#define SwTrunk4 4                                    // number of the 4th trunk switch (active if a fourth ball is in the trunk) - set to 0 if machine has only three balls
#define SwLeftOutlane 5                               // number of the left outlane switch
#define SwRightOutlane 6                              // number of the right outlane switch
#define SolACrelay 7                                  // number of the AC relay solenoid (set to 0 if machine has no AC relay)
#define SolLeftKickback 8                             // number of the left kickback solenoid (set to 0 if machine has no left kickback)
#define SolRightKickback 9                            // number of the right kickback solenoid (set to 0 if machine has no right kickback)
#define SolOuthole 10                                 // number of the outhole kicker solenoid
#define SolShooterLn 11                               // number of the shooter lane feeder solenoid (set to 0 if machine has no shooter lane feeder (only one ball)
#define LampExBall 12                                 // number of the extra ball lamp (on the playfield) which is supposed to blink when ball saver is active

const byte EX_SpaceStationProperties[13] = {          // machine properties for ball saver
    10,                                               // number of the outhole switch
    11,                                               // number of the 1st trunk switch (active if one ball is in the trunk) - set to 0 if machine has only one ball (-> no trunk)
    12,                                               // number of the 2nd trunk switch (active if a second ball is in the trunk)
    13,                                               // number of the 3rd trunk switch (active if a third ball is in the trunk) - set to 0 if machine has only two balls
    0,                                                // number of the 4th trunk switch (active if a fourth ball is in the trunk) - set to 0 if machine has only three balls
    17,                                               // number of the left outlane switch
    32,                                               // number of the right outlane switch
    12,                                               // number of the AC relay solenoid (set to 0 if machine has no AC relay)
    13,                                               // number of the left kickback solenoid (set to 0 if machine has no left kickback)
    0,                                                // number of the right kickback solenoid (set to 0 if machine has no right kickback)
    1,                                                // number of the outhole kicker solenoid
    2,                                                // number of the shooter lane feeder solenoid (set to 0 if machine has no shooter lane feeder (only one ball)
    42};                                              // number of the extra ball lamp (on the playfield) which is supposed to blink when ball saver is active

const byte EX_WhirlwindProperties[13] = {
    10, 13, 12, 11, 0, 17, 16, 12, 0, 0, 1, 2, 57};

const byte EX_GorgarProperties[13] = {
    9, 0, 0, 0, 0, 10, 34, 0, 0, 0, 1, 0, 1};

const byte EX_AlienPokerProperties[13] = {
    9, 0, 0, 0, 0, 11, 32, 0, 0, 0, 1, 0, 1};

const byte EX_BarracoraProperties[13] = {
    12, 15, 14, 13, 0, 23, 24, 0, 0, 0, 11, 12, 26};

const byte EX_BlackKnightProperties[13] = {
    20, 17, 18, 19, 0, 11, 12, 0, 0, 0, 1, 6, 47};

const byte EX_CometProperties[13] = {
    45, 0, 0, 0, 0, 32, 31, 0, 0, 0, 1, 0, 60};

const byte EX_DiscoFeverProperties[13] = {
    22, 0, 0, 0, 0, 25, 19, 0, 0, 0, 1, 0, 33};

const byte EX_FirepowerProperties[13] = {
    9, 57, 58, 51, 0, 10, 44, 0, 7, 0, 1, 8, 1};
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

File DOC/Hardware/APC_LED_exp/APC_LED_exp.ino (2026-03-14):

#include "Arduino.h"
#include <Adafruit_NeoPixel.h>
#ifdef __AVR__
#include <avr/power.h>
#endif
#define PIN            12                               // change to 16 for Arduino Nano

byte RecByte = 0;                                       // received byte
bool RecFlag;
byte LampStatus[24];                                     // current status of each lamp
byte LampMax[192][3];                                    // current max color values of each lamp
byte LampMaxSel[3] = {200, 200, 200};                   // selected max color values
byte Sync = 8;                                          // ms after last Sync
byte Mode = 0;                                          // Mode 0 -> lamps being lit get the ColorSelect color / Mode 1 -> lamps keep their color / Mode 2 -> lamps set in the following frame get the new color immediately
byte Command = 0;                                       // LED command currently being processed
byte CommandCount = 0;                                  // counts the bytes received by the color select command
byte SystemFlags = 0;                                   // to indicate special system states
byte OwnCommands = 0;                                   // indicate active own LED commands
byte OwnCommandStep = 0;                                // needed for own LED commands
byte NumOfLEDbytes = 8;                                 // stores the length of the transferred LED pattern
byte TurnOn[6][24];                                      // the list of the lamps currently being turned on
byte TurnOff[6][24];                                     // the list of the lamps currently being turned off
Adafruit_NeoPixel pixels = Adafruit_NeoPixel(NumOfLEDbytes*8, PIN, NEO_GRB + NEO_KHZ800);
const byte OwnPattern[6][3] = {{0,0,0},{0,50,0},{0,100,0},{0,150,0},{0,200,0},{0,250,0}};

void setup() {
  pixels.begin();
  for (byte i=0;i<9;i++) {
    pinMode(i, INPUT_PULLUP);}
  pinMode(13, OUTPUT);
  pinMode(10, OUTPUT);
  for (byte i=0;i<64;i++) {
    for (byte c=0;c<3;c++) {
      LampMax[i][c] = 255;}}
  RecFlag = PINB && 1;}

void loop() {
  if ((PINB & 1) != RecFlag) {                          // get byte
    RecByte = PIND;                                     // store it
    RecFlag = !RecFlag;
    digitalWrite(13, RecFlag);
    if (Sync < NumOfLEDbytes) {                         // still LED pattern bytes to transfer?
      if (Mode < 2) {                                   // LEDs fade on and off
        for (byte c=0;c<5;c++) {                        // for 5 brightness levels
          if (TurnOn[c][Sync]) {                        // anything to do in this byte?
            byte Mask = 1;                              // initialize bitmask
            for (byte i=0;i<8;i++) {                    // for the 8 lamps currently being processed
              if (TurnOn[c][Sync] & Mask) {
                if (c) {
                  pixels.setPixelColor(Sync*8+i, pixels.Color(LampMax[Sync*8+i][0]/5*(5-c),LampMax[Sync*8+i][1]/5*(5-c),LampMax[Sync*8+i][2]/5*(5-c)));}
                else {                                  // for the last level turn it fully on
                  pixels.setPixelColor(Sync*8+i, pixels.Color(LampMax[Sync*8+i][0],LampMax[Sync*8+i][1],LampMax[Sync*8+i][2]));}}
              Mask = Mask << 1;}}
          TurnOn[c][Sync] = TurnOn[c+1][Sync];
          if (TurnOff[c][Sync]) {
            byte Mask = 1;                              // initialize bitmask
            for (byte i=0;i<8;i++) {                    // for the 8 lamps currently being processed
              if (TurnOff[c][Sync] & Mask) {
                if (c) {
                  pixels.setPixelColor(Sync*8+i, pixels.Color(LampMax[Sync*8+i][0]/5*(c),LampMax[Sync*8+i][1]/5*(c),LampMax[Sync*8+i][2]/5*(c)));}
                else {                                  // for the last level turn it completely off
                  pixels.setPixelColor(Sync*8+i,pixels.Color(0,0,0));}}
              Mask = Mask << 1;}}
          TurnOff[c][Sync] = TurnOff[c+1][Sync];}
        if (RecByte != LampStatus[Sync]) {              // any status changes?
          byte Mask = 1;                                // initialize bitmask
          for (byte i=0;i<8;i++) {
            if ((RecByte & Mask) && !(LampStatus[Sync] & Mask)) { // lamp turned on
              if (Mode == 0) {                          // New lit lamps get a new color
                for (byte c=0;c<3;c++) {                // set max brightness of lamp to selected max value
                  LampMax[Sync*8+i][c] = LampMaxSel[c];}}
              LampStatus[Sync] |= Mask;
              TurnOn[5][Sync] |= Mask;}
            else {
              TurnOn[5][Sync] &= (255 - Mask);}
            if (!(RecByte & Mask) && (LampStatus[Sync] & Mask)) { // lamp turned off
              LampStatus[Sync] &= (255 - Mask);
              TurnOff[5][Sync] |= Mask;}
            else {
              TurnOff[5][Sync] &= (255 - Mask);}
            Mask = Mask << 1;}}
        else {
          TurnOn[5][Sync] = 0;
          TurnOff[5][Sync] = 0;}}
      else {                                            // Mode > 1
        if (Mode < 4) {                                 // selected lamps get the selected color immediately
          if (RecByte) {                                // any lamps set?
            byte Mask = 1;
            for (byte i=0;i<8;i++) {                    // for the 8 lamps currently being processed
              if (RecByte & Mask) {                     // lamp set in RecByte?
                if (Mode == 2)  {                       // selected LEDs are also turned on
                  for (byte c=0;c<5;c++) {              // and 5 brightness levels
                    TurnOn[c][Sync] &= (255 - Mask);    // stop lamp from TurningOn - Off
                    TurnOff[c][Sync] &= (255 - Mask);}
                  LampStatus[Sync] |= Mask;             // turn on lamp
                  pixels.setPixelColor(Sync*8+i, pixels.Color(LampMaxSel[0],LampMaxSel[1],LampMaxSel[2]));}
                else {                                  // Mode = 3
                  if (LampStatus[Sync] & Mask) {        // LED on?
                    pixels.setPixelColor(Sync*8+i, pixels.Color(LampMaxSel[0],LampMaxSel[1],LampMaxSel[2]));}}
                for (byte c=0;c<3;c++) {                // set max brightness of lamp to selected max value
                  LampMax[Sync*8+i][c] = LampMaxSel[c];}}
              Mask = Mask << 1;}}}}
      if (!Sync && OwnCommands) {                       // a good place to let an own command run once per refresh cycle
        if (OwnCommands & 1) {                          // check which command is meant
          if (!(OwnCommandStep % 5)) {                  // only be active every 5th refresh cycle
            byte Step = OwnCommandStep / 5;             // calculate the current step
            for (byte i=0;i<6;i++) {                    // pattern has 6 fading grades
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

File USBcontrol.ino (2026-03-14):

// USB interface for APC based pinball machines

const byte USB_CommandLength[110] = {0,0,0,0,0,0,0,1,0,0,   // Length of USB commands from 0 - 9
                              1,1,1,0,0,0,0,0,0,0,    // Length of USB commands from 10 - 19
                              1,1,1,1,2,2,0,0,0,0,    // Length of USB commands from 20 - 29
                              250,250,250,250,250,0,0,2,0,0,    // Length of USB commands from 30 - 39
                              1,0,0,0,0,0,0,0,0,0,    // Length of USB commands from 40 - 49
                              2,1,251,0,2,0,0,0,0,0,  // Length of USB commands from 50 - 59
                              10,0,0,0,2,3,0,0,0,0,   // Length of USB commands from 60 - 69
                              0,0,0,0,0,0,0,0,0,0,    // Length of USB commands from 70 - 79
                              2,1,2,0,0,0,0,0,0,0,    // Length of USB commands from 80 - 89
                              0,0,0,0,0,0,0,0,0,0,    // Length of USB commands from 90 - 99
                              0,0,0,0,0,0,0,0,0,0};   // Length of USB commands from 100 - 109
const byte USB_DisplayDigitNum[9][6] = {{4,7,7,7,7,0},{4,7,7,7,7,0},{0,7,7,7,7,0},{0,16,16,0,0,0},{0,16,16,0,0,0},{0,16,16,7,0,0},{0,16,16,7,4,0},{4,6,6,6,6,0},{4,7,7,7,7,0}};
const byte USB_DisplayTypes[9][6] = {{3,4,4,4,4,0},{3,4,4,3,3,0},{0,4,4,3,3,0},{0,4,4,0,0,0},{0,4,4,0,0,0},{0,4,3,3,0,0},{0,4,3,3,3,0},{1,1,1,1,1,0},{1,2,2,2,2,0}};

                                                      // offsets of settings in the settings array
#define USB_Watchdog 0                                // watchdog enable setting
#define USB_Debug 1                                   // USB debug mode
#define USB_PinMameSound 2                            // use APC sound HW or old sound board?
#define USB_PinMameGame 3                             // number of the game to be run in PinMame
#define USB_LisyDebug 4                               // selected debug mode
//#define USB_BallSave 5                              // optional ball saver -> this option is defined in PinMameExceptions.ino
//#define USB_BallSaveTime 6                          // activation time for the optional ball saver -> this option is defined in PinMameExceptions.ino
//#define USB_BGmusic 7                               // to select an own BG music -> this option is defined in PinMameExceptions.ino
#define USB_RecycleSolenoid1 8                        // number of the solenoid to select a recycling time of 250ms for
#define USB_RecycleSolenoid2 9
#define USB_RecycleSolenoid3 10
#define USB_RecycleSolenoid4 11

const byte USB_defaults[64] = {0,0,0,255,0,0,20,0,    // game default settings
                              0,0,0,0,0,0,0,0,
                              0,0,0,0,0,0,0,0,
                              0,0,0,0,0,0,0,0,
                              0,0,0,0,0,0,0,0,
                              0,0,0,0,0,0,0,0,
                              0,0,0,0,0,0,0,0,
                              0,0,0,0,0,0,0,0};
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

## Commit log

2018-02-04 Comments for LED handling added
2018-02-09 Solenoid numbers corrected for APC V2
    [APC.ino, BlackKnight.ino]
2018-02-09 Special solenoid treatment added
2018-02-10 Bugfix LED implementation
2018-02-10 Bugfix LED handling 2
    [APC.ino]
2018-02-11 Bugfix LED handling 3
    [APC.ino]
2018-02-12 Timing of LED control relaxed for exp board
2018-02-13 LED protocol changed to 1 byte per cycle
2018-02-15 Lamp handling moved to the end of the IRQ to relax LED exp timing
2018-02-24 Sol times and LowerNum pattern corrected
    [APC.ino, Pinbot.ino]
2018-03-17 Bugfixes in Pinbot and cleanups in BK
    [APC.ino, BlackKnight.ino, Pinbot.ino]
2018-04-25 A/C handling improved Bugfix in planet lamp handling
    [APC.ino, Pinbot.ino]
2018-06-06 Revert "Cleanups and some lightshow added to Pinbot's chest"
    This reverts commit a832915da9e979d44747e3043f6d3ce166e9f2c2.
    [APC.ino, BlackKnight.ino]
2018-06-11 Bugfix Chestlight. Display Patterns changed
    [APC.ino, Pinbot.ino]
2018-07-03 Chest switch functionality added
2018-07-03 more chest switch functionality added
2018-07-03 Eject hole handling started
2018-07-04 Bugfix - timer and switch event handling changed to avoid IRQ interference
    [APC.ino]
2018-07-16 chest light management reworked and some eject hole stuff added
    [APC.ino, Pinbot.ino]
2018-08-19 Debug button added
2018-09-15 Bus timing relaxed to avoid mistriggering of slow latches
    [APC.ino]
2018-09-28 LED control changed
2018-10-05 2nd audio track handling added
2018-11-18 made some more char* constant (globals and in structs) to avoid compiler warnings
    [APC.ino]
2018-11-18 introduced UNUSED macro to avoid "unused parameter" warning
    [APC.ino, BlackKnight.ino, Pinbot.ino]
2018-11-18 fixed array initialization warnings
    [APC.ino, BlackKnight.ino, Pinbot.ino]
2018-11-21 Bugfixes and some more effects
    [APC.ino, BlackKnight.ino, Pinbot.ino]
2018-12-04 A/C solenoid scheduler implemented
2018-12-09 PB_EyeBlink added. Initials handling reworked.
    [APC.ino, Pinbot.ino]
2018-12-09 BlinkScoreTimer removed Indentation auto corrected
    [APC.ino, BlackKnight.ino, Pinbot.ino]
2018-12-10 Blink score duty cycle corrected
    [APC.ino]
2018-12-11 File not found error added
    [APC.ino, Pinbot.ino]
2018-12-17 LockChaseLight changed to static timer variable
2018-12-29 APC: Bugfix ShowNumber / Pinbot: ball saver option added
    [APC.ino, Pinbot.ino]
2019-01-06 Bugfix LED control
2019-01-28 documents added
    [APC-B.Cu.gbr, APC-F.Cu.gbr, APC-PTH.drl]
2019-03-09 Docs added
    [APC_LED_exp-B.Cu.gbr, APC_LED_exp-PTH.drl]
2019-03-15 BOM added
2019-03-31 Base Code implemented
    [APC-B.Mask.gbr, APC-B.SilkS.gbr, APC-F.Mask.gbr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]
2019-04-05 Old Gerber files removed
    [APC-B.Cu.gbr, APC-B.Mask.gbr, APC-B.SilkS.gbr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]
2019-04-05 New Gerber files added and drill holes of audio amp enlarged
2019-04-07 Gerber files updated
2019-04-07 Sys7Alpha gerber files cleanup
    [Alpha_v11_-Bottom.gbr, Alpha_v11_-PTH.drl, Credit_v11_-Bottom.gbr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]
2019-04-12 Amok work (#11)
    * USB control first draft
    * USB data transfer implemented
    * USB commands finalized
    * Bugfix USB control
    [APC.ino, USBcontrol.ino]
2019-04-24 Amok work (#12)
    * Numerical display support first draft
    * Menu support for num displays added
    * Preparations for num commas
    * USB control almost finished
    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
    [APC.ino, USBcontrol.ino]
2019-05-01 Lamp and switch handling changed
    * Switch handling changed
    * Switch handling change completed
    * Lamp handling changed
    * Lamp patterns changed
    * All lamp patterns adapted to the new scheme
    * Changes in switch and lamp handling finalized
    * Bugfix switch handler
    * Solenoid 25 added
    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
    [APC.ino, BaseCode.ino, BlackKnight.ino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]
2019-05-18 Bugfix switch buffer overflow
    [APC.ino]
2019-05-19 Bugfix Soundcheck
    * Bugfix menu selector
    * Bugfix main loop
    * Bugfix switch buffer overflow
    * Bugfix SoundCheck
    * Bugfix HandleNumSetting
    [APC.ino, APC_SoundCheck.ino]
2019-05-22 BOM of Sys7Alpha updated
2019-05-22 BOM update 2nd try
2019-05-22 Bugfix Soundcheck.ino
    * Pinbot eye bugfix
    * BOM of Sys7Alpha updated
    * BOM update 2nd try
    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
    [Pinbot.ino, Rollergames.ino]
2019-05-24 Switch handler removed
2019-06-07 Connectors pic added
2019-06-08 BOM updated
2019-06-09 USB watchdog disable bugfix
    [Tutorial.ino, USBcontrol.ino]
2019-06-12 Bugfix: Number of switches increased to 73. Version increased to 0.02.
    [USBcontrol.ino]
2019-06-13 Number of lamps corrected
    [USBcontrol.ino]
2019-06-15 100nF footprints corrected
2019-06-15 Bugfix Basecode solenoid test and usb_control flipper enable
    [BaseCode.ino, USBcontrol.ino]
2019-06-15 Bugfixes
    * Number of lamps corrected
    * Watchdog command number changed
    * 100nF footprints corrected
    * Bugfix Basecode solenoid test and usb_control flipper enable
    [BaseCode.ino, USBcontrol.ino]
2019-06-20 Bugfix activation of ShowLampPatterns
    [Pinbot.ino]
2019-06-20 Revert "ShowLampPattern changed"
    This reverts commit 3e0a8ace0558435bc5d59707a3848385362cfea6.
    [APC.ino]
2019-06-20 MPF support and DOCs improved
    * USBcontrol adapted to MPF
    * ByteBuffer3 removed from ShowLampPatterns
    * Bugfix activation of ShowLampPatterns
    * ShowLampPattern description updated
    * ShowLampPattern changed
    * Revert "ShowLampPattern changed"
    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
    [APC.ino, BaseCode.ino, BlackKnight.ino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]
2019-09-22 V00.12
    * Lisy 0.09 implemented
    * Tutorial added
    * Drop targets added
    * Back to the normal AttractMode
    * Bugfix USBcontrol
    * Connectors pic added
    * Layout updates
    * Attract mode restored
    * BOM updated
    * Hardware rules implemented
    * HW rules fine tuning
    * HW rules finalized?
    * USB watchdog option added
    * USB watchdog disable bugfix
    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
    [machine_vars.yaml]
2019-12-02 Migrated from KiCad 3
2019-12-06 Multiball visor issue fixed
    [Pinbot.ino]
2019-12-18 Bugfix: wrong switch number was used to check outhole in BallEnd
    [BlackKnight.ino]
2019-12-19 Sys7Display Gerber Files uploaded
2019-12-19 Sys7Display schematics and BOM added
    [S7Driver20p_BOM.csv]
2020-02-08 Solenoid delay removed for ActivateSolenoid
2020-02-28 Bugfix solenoid driver and BOM
    [APC.ino]
2020-02-28 LED_exp code added
2020-03-12 HW_ext rework part 1
    [APC.ino]
2020-03-13 Revert "HW_ext rework part 1"
    This reverts commit c849b7071d6cda616fb6ed39727335d39724afba.
    [APC.ino]
2020-03-15 HwExt rework next try
    [APC.ino]
2020-04-13 Solenoid expander added
    [APC_Solenoid_exp-B.Cu.gbr, APC_Solenoid_exp-B.Mask.gbr, APC_Solenoid_exp-B.Paste.gbr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]
2020-04-14 Bugfix: missing sound after StopSound
    [APC.ino, USBcontrol.ino]
2020-04-17 MPF files updated
    [machine_vars.yaml]
2020-04-19 Default solenoid times changed in BaseCode
2020-04-25 V00.13 (#25)
    * version number increased
    * First sounds implemented
    * Basic sound done
    * Play drop target sound faster
    * Sound stuff
    * Small sound fixes
    * Default game changed to USBcontrol
    * Migrated from KiCad 3
    * Multiball visor issue fixed
    * Eagle version of S7_Display data added
    * Bugfix: wrong switch number was used to check outhole in BallEnd
    * Sys7Display Gerber Files uploaded
    * Sys7Display schematics and BOM added
    * Cosmetic change
    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
    [S7Driver20p_BOM.csv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]
2020-12-20 V00.14 (#27)
    * Merge confilcts resolved
    * Version number increased. Bugfix: sol 22 ignored in test mode
    * BC_SolTim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
    [APC_BOM.csv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]
2021-01-02 V00.21 (#29)
    * component annotations changed
    * Return value for number of lamps increased to 65
    * New multiball started
    * Multiball sequence tried
    * Multiball bugfix
    * Multiball start...
    * Multiball start done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
    [lisyminigames.csv]
2021-06-02 V00.22 (#30)
    * USB sound debugging changed
    * BK turnaround handling changed
    * variable cleanup
    * Add game specific sound handling for Pharaoh
    * Exception handling changed 1st try
    * Bugfix sound exceptions
    * More exceptions added first try
    * More exceptions final
    * BK exceptions added
    * Pharaoh exceptions and DOCs added
    * Typos fixed
    * Pharaoh added
    * Bugfix Pharaoh sound numbers
    * Typos and rephrasing
    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
    [APC_BOM.csv, lisyminigames.csv]
2022-07-22 V00.23 (#33)
    * Rollergames tweaking
    * More RG tweaking
    * Column setting for attract mode lamps added
    * Lamp columns added in DOCs
    * Bugfix backbox lamps column
    * Readme update
    * Bugfix Sys11 audio board
    * Started to revert Pinbot sounds to original
    * Number of active timers added for numerical displays
    * Pinbot Bonus rewrite started
    * Bonus effects added
    * Bonus Multiplier effect added
    * Bugfix PlayFlashSeq started
    * BugFix ActSol 1
    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
    [APC_BOM.csv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]
2022-07-24 Almost forgot Data East
    [lisyminigames.csv]
2022-08-06 V00.30 (#36)
    * Tried in vain to fix the PB_LitChestLamps
    * Bugfix PB_LitChestLamps
    * Bugfix PB_ShowMessage
    * Bugfix USB interface in OnBoard comm mode.
    * Bugfix Error 11 at end of PinMame game
    * DOC update
    * typo
    [APC.ino, Pinbot.ino, USBcontrol.ino]
2023-03-17 V00.31 (#38)
    * SD adapter added to HW version 3.1
    * Molex connectors moved and MOSFETs rotated
    * Sol recycle time feature included in Activate-/Release-Solenoid
    * Footprint of SD adapter corrected
    * Bugfix Comet music stop command in PinMameExceptions
    * 2nd bugfix of the Comet music stop command
    * Fabrication files updated
    * LED_exp board outline missing
    * Pinbot music test changed
    * Started to add num display support to BK
    * New score blinking first try
    * Upgrade score blinking
    * Bugfix Score blinking
    * Support for Sys7 displays added to BlinkScore
    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
    [APC_BOM.csv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]
2023-12-11 V01.00 (#40)
    * Rev number set to 1.00
    * jackpot effects integrated
    * Bugfix Sound/Music priorities
    * Backbox effects finalized
    * Audio select signals for System 3 - 6 inverted
    * 3 ball multiball the 3rd
    * 3 ball multiball
    * 3 ball multiball playable
    * PinMameExceptions for Flash changed
    * Sys 3 - 6 audio board commands reworked
    * Bugfix Sys 3 - 6 audio board commands
    * Indentation of Firepower exceptions changed to spaces
    * Support for single ball games added to BC
    * ClearOutLock fixed
    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
    [lisyminigames.csv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]
2023-12-23 C14 increased
    [APC_BOM.csv]
2024-06-26 V01.01 (#42)
    * New attract mode animations started
    * Space Station added
    * Support for Space Station added
    * Non working fix to improve MusicVolume
    * Bugfix MusicVolume
    * Space Station fine tuning
    * PB_SearchBall improvements
    * A bit more Space Station fine tuning
    * Bugfix PB multiball display
    * PB minor improvements
    * 3 Mball music improvements
    * PB_SearchBall improvements
    * Space Station fine tuning
    * PB_ClearOutLock improved
    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
    [APC_BOM.csv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]
2024-11-19 V01.02 (#43)
    * Time warp BG sound fine tuning
    * Ball Saver for High Speed - first try
    * General Ball Saver - first try
    * Space Station Ball saver - slightly better
    * Bugfix Ball Saver
    * Ball Saver RelSwitch exceptions added
    * Bugfix High Speed Ball Saver
    * AC handling added to ball saver
    Merge branch 'master' of https://github.com/AmokSolderer/APC.git into
    V01.02
    * Bugfix BallSaver AC handling
    * More ball saver issues
    * Ball Saver Space Station working
    * Still Ball Saver improvements
    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
    [APC.ino, BaseCode.ino, PinMameExceptions.ino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]
2025-06-09 V01.03 (#45)
    * Bugfix BK BonusCount
    * Still not done with BK BonusCount
    * Firepower Bonus counting fixed
    * Variable cleanup: global counter i removed
    * New setting to select the connection type on startup implemented
    * Send two zeroes as a reply to command 19 (get number of modern lights)
    * Changelog updated
    * Loop cleanup
    * PB_MballDisplay protected against double calls
    * Larger high scores for 4Alpha + Credit display implemented
    * 2nd loop cleanup
    * Timer interrupt disabled in critical loop areas
    * Revert "Timer interrupt disabled in critical loop areas"
    This reverts commit b0a3d21d8e8f830a1084d41eb3736bb80d4be96d.
    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
    [APC.ino, BaseCode.ino, BlackKnight.ino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]
2026-03-14 V01.04 (#49)
    * Setup 1.04 branch
    * Changes for special APC display implemented
    * Bugfix initials on lower alpha displays
    * Superfluous PB_ShowBigScores removed
    * Display of high scores >=10M enabled for BK also
    * Links added to audio files
    * Tri Zone added
    * Draft exceptions for Whirlwind added
    * Support for Sound Overlay Solenoid Board added
    * Use of HwExt interface optimized to reduce distortion
    * Special solenoids disabled when flippers are off
    * F-14 exceptions fine tuning
    * USB debug log implemented
    * F-14: recycle times for slingshots added
    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
    [APC_Solenoid_exp2_bom.csv, Disp_Sys11a_bom.csv, DisplayBK2k_BOM.csv]
